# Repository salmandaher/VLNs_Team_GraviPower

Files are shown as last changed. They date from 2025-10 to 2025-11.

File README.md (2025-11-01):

# Solid-Gravity-Energy-Storage-System
Robotic Gravity-based energy storage system designed for smart cities — converts vehicle motion into storable mechanical energy and regenerates it electrically through controlled descent.

# Project Video and Report

Below is the high-quality version of the video we submitted to the WRO competition, showcasing our project in action.  
[WRO Competition Video](https://youtu.be/KDbOAnvwZOE)

You can also download and review the detailed project report we submitted:  
**[Project Report (WRO Submission)](https://github.com/salmandaher/VLNs_Team_GraviPower/blob/bfb26dfb872fea5c6c9b23eaee99e1bb86ba5fde/final%20report%20-%20VLNs.pdf)**

---

# Hi from the VLNs Team!

Welcome to our project repository. We are the VLNs team, passionate about robotics and innovation.

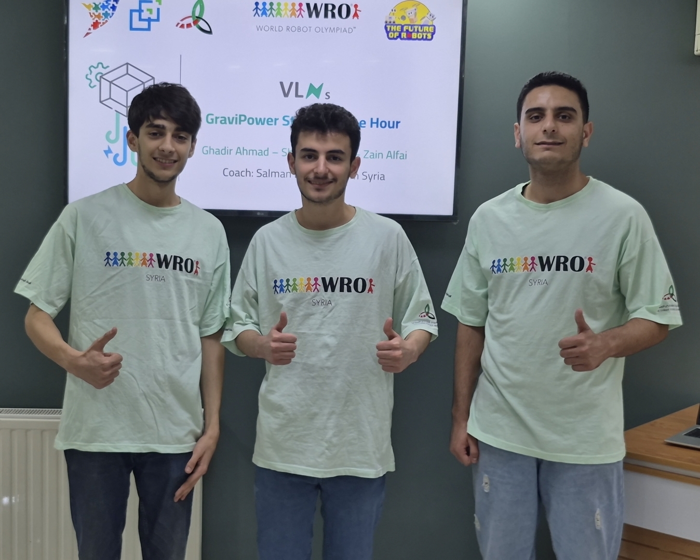
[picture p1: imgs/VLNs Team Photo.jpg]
Team Photo


Here is our coach, who has been a great mentor and guide throughout our journey:

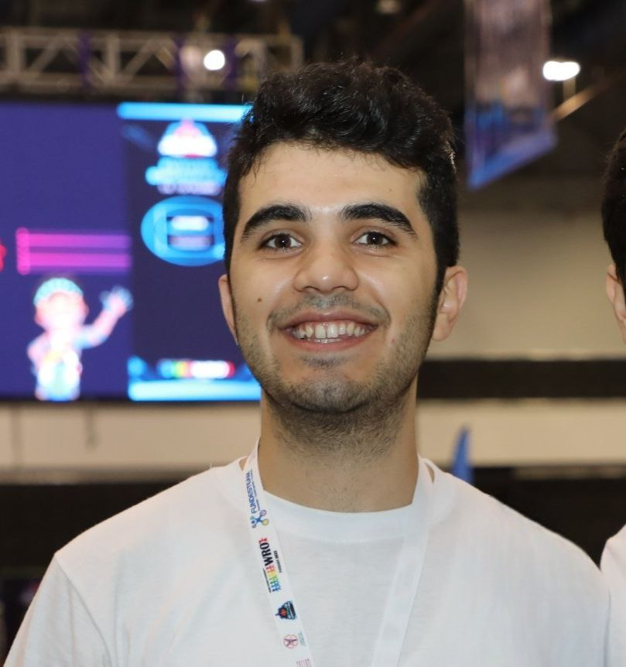
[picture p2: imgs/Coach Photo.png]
Coach Photo


---

# Full Project Photo

Full Project Photo

---

# Mechanism Design

This section provides an overview of the key mechanical components used in our project. Each mechanism plays a crucial role in ensuring efficient operation and durability. The associated STL files for 3D printing or modeling are included in the repository.

## Pseudo-Bump Mechanism Overview

The pseudo-bump functions by converting the mechanical energy from vehicles passing over it into usable energy for the system. It includes several key components that work in harmony to achieve this. The fixed joint acts as the pivot point for the bump's rotation when a vehicle passes over it. Inside this joint is an anti-reverse bearing (Rollman bearing) that prevents backward motion when the bump resets. Once a car passes, a return spring compresses under pressure and then pushes the bump back to its starting position when the vehicle leaves. The moving joint allows the bump to flatten as vehicles pass, transferring the force efficiently through the rotation of the fixed joint and maintaining system reliability.

### Fixed Joint

This contains two STL parts: the connecting plate, which connects the fixed joint to the moving joint, and the bearing holder that houses the bearing linked to the Tetrix system.  
**STL files:**  
- [First Part (Fixed Joint) STL](https://github.com/salmandaher/VLNs_Team_GraviPower/blob/d1e83de02112018f51a4b01dffcafd82a4864781/3d%20designs/Bump/first.stl)  
- [Bearing Holder STL](https://github.com/salmandaher/VLNs_Team_GraviPower/blob/d1e83de02112018f51a4b01dffcafd82a4864781/3d%20designs/stls/inner%20bearing%20to%20tetrix.stl)  

### Moving Joint

The moving joint is created between the plate with the fixed joint and another plate with a free end, which part pressed directly by vehicles.  
**STL file:**  
- [Moving Joint Linkage STL](https://github.com/salmandaher/VLNs_Team_GraviPower/blob/d1e83de02112018f51a4b01dffcafd82a4864781/3d%20designs/Bump/second.stl)  

### The Base

This holds the fixed and moving joints together, providing structural stability.  
**STL file:**  
- [Base Station STL](https://github.com/salmandaher/VLNs_Team_GraviPower/blob/d1e83de02112018f51a4b01dffcafd82a4864781/3d%20designs/Bump/station.stl)  

### Bump Motion Description

The bump moves when the free end is depressed by a passing vehicle, rotating around the fixed joint. After the vehicle passes, the return spring restores the bump to its original raised position, completing the motion cycle.

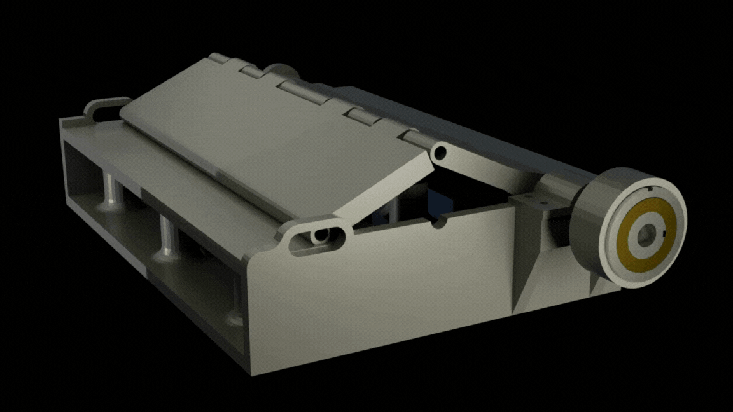
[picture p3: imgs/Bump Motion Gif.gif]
Bump Movement


---

## Motion Transmission and Torque Amplification (The Gearbox)

This part of the project is critical as it ensures efficient transfer and amplification of the torque necessary to lift the mass. The total torque amplification ratio achieved here is 10:1, an essential factor for the prototype’s performance. The motion transmission is divided into two main steps, each playing a specific role in the mechanism.

### Gearbox 

The first stage involves a gearbox with a 4:1 gear speed ratio, providing speed amplification (which is a 1:4 torque ratio). This speed amplification factor is necessary to counter the huge torque amplification factor of the next stage, keeping the torque amplification high just enough to lift the mass with the weight of the passing car.

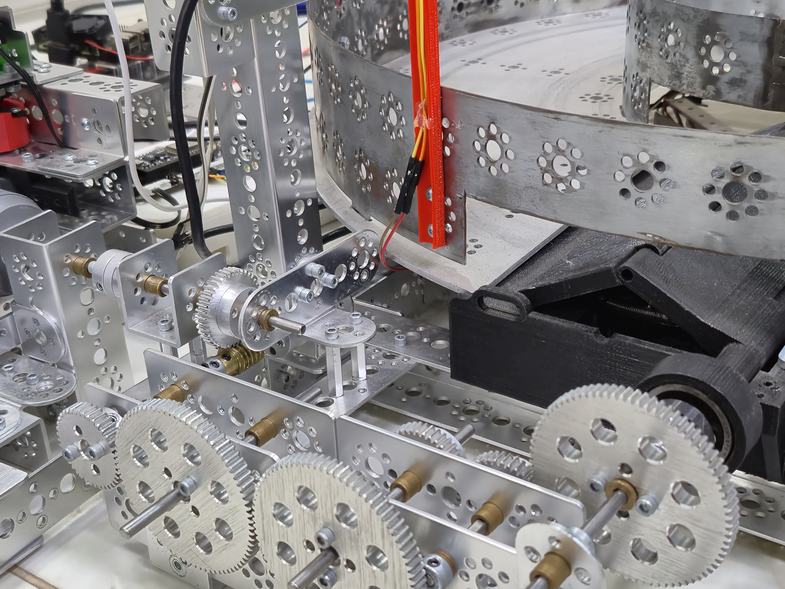
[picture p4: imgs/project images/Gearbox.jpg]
Gearbox image
 

### Worm Gear 

The second stage is a worm gear, which serves two main purposes. First, it amplifies torque with a 40:1 ratio, making it easier for the car to press the bump. Second, the worm gear acts as a self-locking mechanism, preventing the mass from falling while being lifted. This is because the worm gear cannot be driven backward by the gear connected to it; it only transmits motion forward, thus securing the mass position reliably.

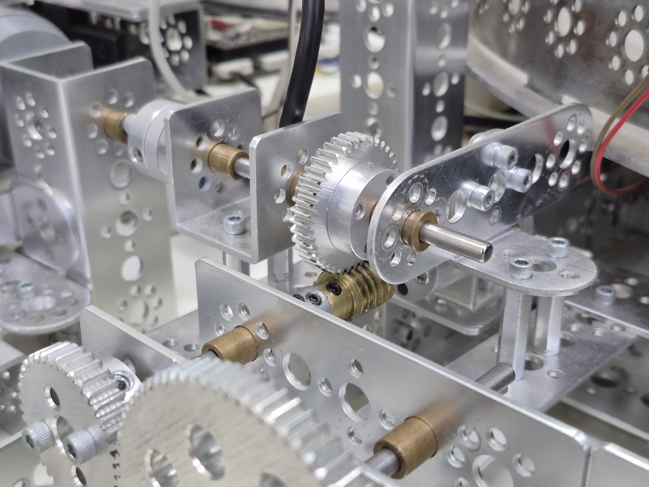
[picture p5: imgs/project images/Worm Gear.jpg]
Worm gear image


---

## Lifting System

The lifting system is responsible for managing the vertical movement of the mass with precision and stability. It consists of three main components:

### Main Pulley (Spool)

This is the central pulley around which the rope winds. Its radius directly affects the torque experienced in the system, playing a key role in the mechanical advantage and energy efficiency. During the project, we designed and tested three main versions of this pulley to optimize performance and durability.

**STL files:**  
- [Version 1 Pulley STL](https://github.com/salmandaher/VLNs_Team_GraviPower/blob/a61094ec972bfa96dd2c8d812677eebc3b2d72a3/3d%20designs/stls/Pulley%20v1.0-01.stl)  
- [Version 2 Pulley STL](https://github.com/salmandaher/VLNs_Team_GraviPower/blob/a61094ec972bfa96dd2c8d812677eebc3b2d72a3/3d%20designs/stls/Pulley%20v1.0-03.stl)  
- [Final Pulley Design STL](https://github.com/salmandaher/VLNs_Team_GraviPower/blob/a61094ec972bfa96dd2c8d812677eebc3b2d72a3/3d%20designs/stls/Pulley%20v3.2.stl) 

### Guiding Pulleys

Two guiding pulleys are installed at the top of the tower. Their main function is to route the rope correctly, ensuring it remains aligned throughout the lifting and lowering operations.

**STL file:**  
- [Guiding Pulley STL](https://github.com/salmandaher/VLNs_Team_GraviPower/blob/a61094ec972bfa96dd2c8d812677eebc3b2d72a3/3d%20designs/stls/direction_pulley.stl)

### Mass Pulley

Attached directly to the mass, this pulley serves multiple purposes: it protects the rope from excessive wear, improves the stability of the mass during motion, and doubles the torque applied when lifting. This crucial component helps regulate the discharge time, improving system reliability.

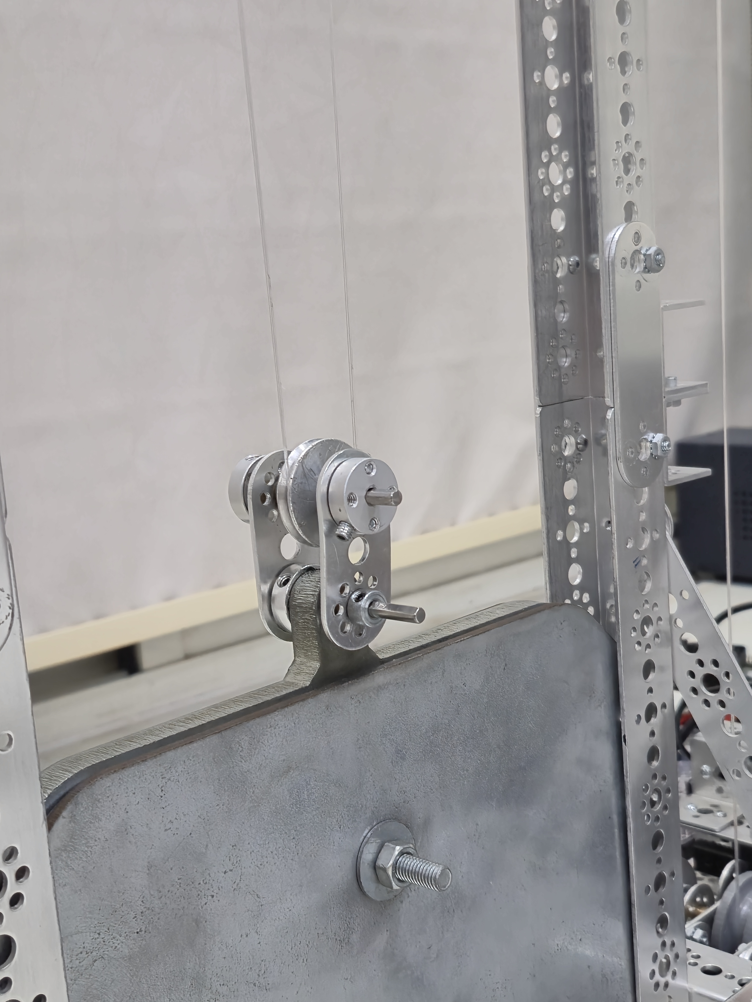
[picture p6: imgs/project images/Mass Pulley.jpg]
Mass pulley image


---

## Connecting and Disconnecting Mechanism

To switch to the discharging mode, the main pulley should be disconnected from the gearbox and connected to the energy generation system, which consists of the motor and its dedicated gearbox. This requirement led to the development of a specialized mechanism for connecting and disconnecting.

The core component consists of 3D-printed PLA parts that resemble circular saw-tooth gears designed to transfer energy unidirectionally. When the main pulley is shifted towards the gearbox side, two opposing saw-tooth parts engage, allowing the gearbox to drive the pulley. Conversely, when the pulley is pushed in the opposite direction, the saw-tooth parts disengage on the gearbox side and engage on the motor side gearbox, thus transferring motion to the motor side.

To facilitate movement between these two positions, we utilize an HTS-35H Servo motor with a torque capacity of 35 kg ·cm. This servo motor is connected to a rack and pinion mechanism that converts the servo’s rotational motion into linear motion, enabling precise and reliable movement of the connecting and disconnecting assembly. The servo is controlled by an ESP32 core board alongside a multifunctional extension board for efficient operation.

### Saw-Tooth Gears

These saw-tooth gears are the key elements that allow unidirectional energy transmission during connection and disconnection. The design includes two complementary halves to ensure smooth engagement and disengagement.

**STL files:**  
- [Saw-Tooth Gear Half 1 STL](https://github.com/salmandaher/VLNs_Team_GraviPower/blob/a61094ec972bfa96dd2c8d812677eebc3b2d72a3/3d%20designs/stls/Coupler%20V2.0-2.stl)  
- [Saw-Tooth Gear Half 2 STL](https://github.com/salmandaher/VLNs_Team_GraviPower/blob/a61094ec972bfa96dd2c8d812677eebc3b2d72a3/3d%20designs/stls/Coupler%20V2.0.stl)

Here is a simulation demonstrating the engagement and disengagement process of the saw tooth gear:
Tooth Gear Motion

### Rack and Pinion Mechanism

The rack and pinion mechanism translates the servo motor’s rotational motion into linear displacement. The pinion, rotated by the servo, engages with the rack teeth to produce controlled linear movement. This mechanism enables the precise shifting required to connect or disconnect the main pulley from either gearbox side.

**STL files:**  
- [Rack STL](https://github.com/salmandaher/VLNs_Team_GraviPower/blob/a61094ec972bfa96dd2c8d812677eebc3b2d72a3/3d%20designs/stls/39300B_TXM-Linear%20Slide%20Rail.stl)  
- [Pinion STL](https://github.com/salmandaher/VLNs_Team_GraviPower/blob/a61094ec972bfa96dd2c8d812677eebc3b2d72a3/3d%20designs/stls/39300A_TXM-Linear%20Slide%20Gear.stl)

Below is a simulation illustrating the full operation of the connecting and disconnecting mechanism:
C&D Full Mechanism Motion

---

## Motor Gearbox
The motor gearbox is set to adjust the motor output speed and torque to a desired level. It applies a 1.5 speed amplification factor, combined with the 2:1 speed amplification applied by the mass pulley system, the total becomes a 3:1 speed amplification factor, rotating the motor from the mass's fall to produce higher voltage values.  

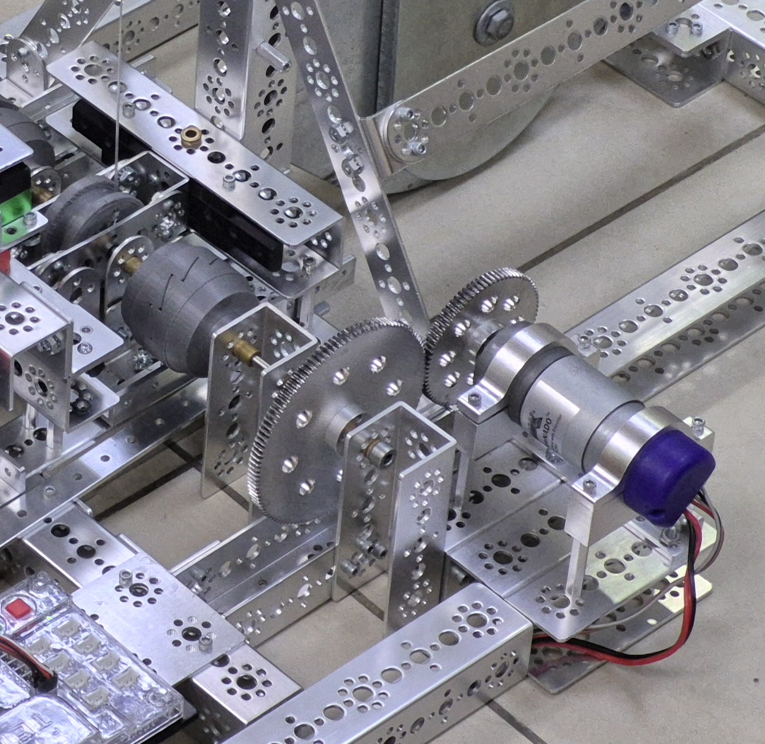
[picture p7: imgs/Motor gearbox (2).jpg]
Motor Gearbox


---

# The coding of the solution
## The main control code (the Python code)

running on the Raspberry Pi 4 device, this Python code serves as the central control unit for our system. It manages the system’s operational states, including charging, discharging, and fast charge modes, by coordinating commands to various controllers such as the PRIZM and the ESP. The code continuously monitors sensor data to make decisions that ensure smooth transitions between modes and optimize system performance. Additionally, it implements a PID control algorithm to regulate the descent speed of the mass, maximizing energy generation efficiency by dynamically adjusting the electrical load without wasting energy through conventional braking. The program also supports real-time monitoring and manual mode control via a connected web-based interface, enabling effective management of the entire energy storage process.

### Main Tasks of the Python Control Code

The Python script performs critical functions to optimize the operation of the gravity-based energy storage system:

1. It calculates the generator's rotational speed during discharging using encoder feedback.
2. It applies a PID (Proportional-Integral-Derivative) control algorithm to regulate the generator speed at the point of maximum power generation efficiency. The PID output is fed to the PWM BTS driver to dynamically adjust the electrical load. The general form of a PID controller is expressed as:

$$
u(t) = K_p e(t) + K_i \int_0^t e(\tau) d\tau + K_d \frac{d e(t)}{d t}
$$

Where:

- $$\( u(t) \) $$ is the control signal output,
- $$\( e(t) \) $$ is the error between target and actual speed,
- $$\( K_p \) $$ is the proportional gain,
- $$\( K_i \) $$ is the integral gain,
- $$\( K_d \) $$ is the derivative gain.

3. It counts the number of vehicles passing over the pseudo-bump to track energy input events.
4. It estimates the current height of the lifted mass by correlating the vehicle count and encoder data using the equation:

$$
h = N_{cars} \times h_{car} - \Delta E \times h_{encoder}
$$

   Where:

   - $$\( h \) $$ is the current height of the lifted mass
   - $$\( N_{cars} \) $$ is the number of cars passing over the pseudo-bump
   - $$\( h_{car} \) = $$ is the height increment per car press (how much one car lifts the mass)
   - $$\( \Delta E \) = $$ is the change in encoder readings during the last discharge
   - $$\( h_{encoder} \) = $$ is the height decrement per encoder pulse (how much one encoder pulse corresponds to the mass descending)

   This equation estimates the net height of the mass by aggregating the lifting increments caused by passing cars
   and subtracting the descent quantified by encoder pulses during discharging.
   
5. Based on the mass height and ambient lighting conditions, it determines the system's operating mode: switching to "maxCharge" when the mass height exceeds 105 units, entering "discharge" mode at night, and defaulting to "charge" or manual mode as selected through the dashboard interface.

### Code Explanation Flowchart
Below is a flowchart illustrating the workflow and main components of the code:

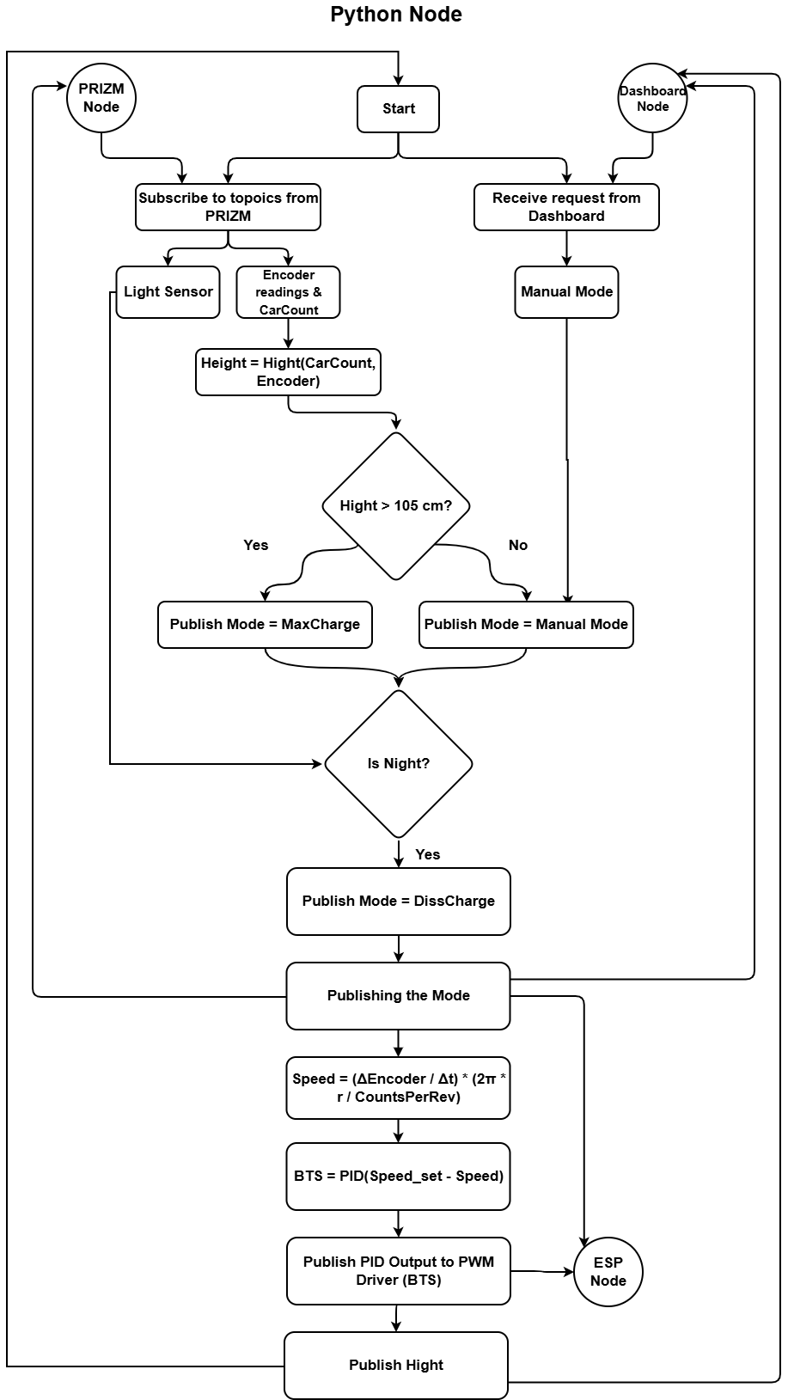
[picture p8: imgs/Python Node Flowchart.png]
Flowchart


### Code
You can view the full code [here](https://github.com/salmandaher/VLNs_Team_GraviPower/blob/main/src/vlns/src/serverna.py).

---

## The PRIZM code:
The PRIZM code is responsible for directly interfacing with hardware components to support the energy storage system's operation. It continuously reads encoder feedback to monitor the generator's rotational position and speed. The code controls the generator, turning it on during the fast charge mode and off during discharging. It detects when a car passes over the pseudo-bump to coordinate energy accumulation events. Furthermore, it manages the servo motor that controls the bump's state, flattening (deactivating) it when not charging and activating it during charging. Lastly, the PRIZM code reads ambient lighting sensor feedback to help determine system modes based on day/night conditions.

### Main tasks of the PRIZM code:

1. Reading encoder feedback for generator monitoring.
2. Controlling the generator state (activated during fast charge mode, deactivated during other modes).
3. Detecting cars passing over the pseudo-bump.
4. Managing the bump-servo motor to flatten or activate the bump based on the mode.
5. Reading the lighting sensor to support automatic mode switching.

### Code Explanation Flowchart
Below is a flowchart illustrating the workflow and main components of the code:

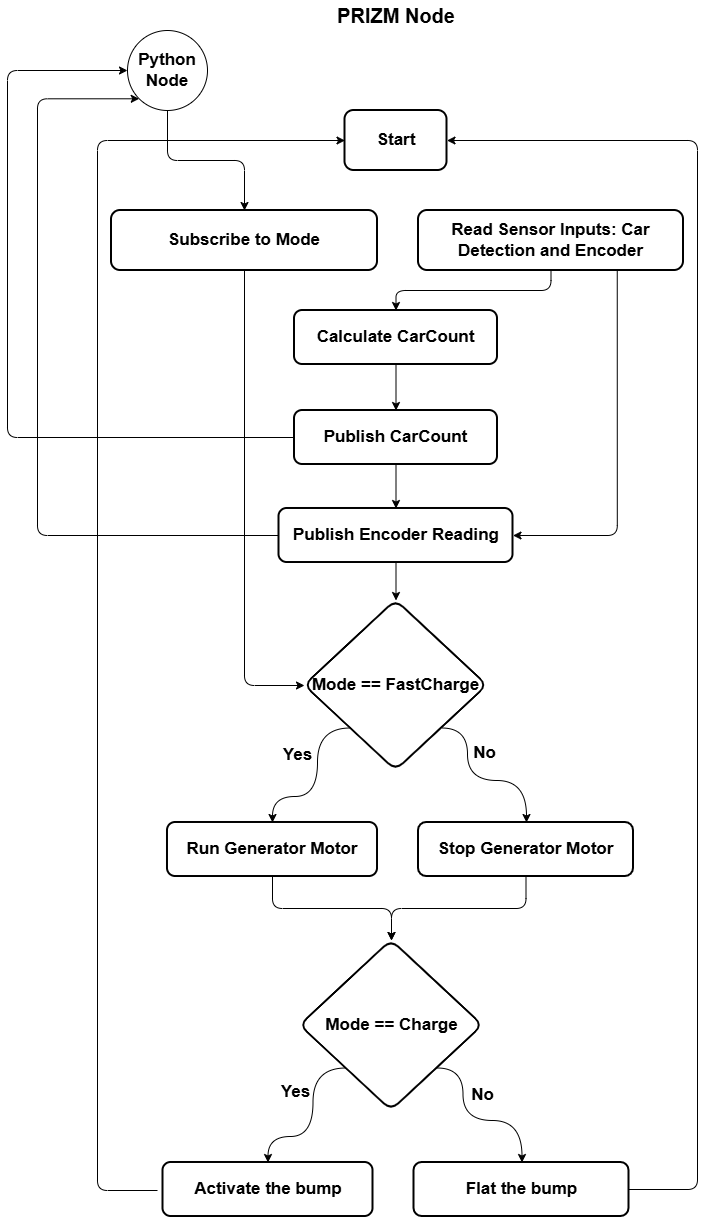
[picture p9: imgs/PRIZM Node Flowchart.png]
Flowchart


### Code
You can view the full code [here](https://github.com/salmandaher/VLNs_Team_GraviPower/blob/main/src/vlns/src/PRIZM_node/PRIZM_node.ino).

---
## The ESP code:
The ESP code functions as the core controller for mechanical and electrical actuations within the energy storage system. It manages the disconnecting and connecting mechanism, dynamically linking the main pulley to the generator during discharge or fast charge modes, and to the gearbox in charge or max charge modes. The code also controls the electrical load system by activating the LED lights during discharge mode and deactivating it otherwise. Furthermore, the ESP code modulates the PWM driver (BTS), adjusting the electrical load on the generator in response to PID control signals computed externally, ensuring precise and efficient energy management.

### Main tasks of the ESP code:

1. Control the disconnecting and connecting mechanism, linking the main pulley to the generator or gearbox based on system mode.
2. Manage the electrical load system indicator light, turning it on only during discharge mode.
3. Regulate the PWM driver (BTS) to adjust the electrical load on the generator using PID output from the Python controller.

### Code Explanation Flowchart
Below is a flowchart illustrating the workflow and main components of the code:

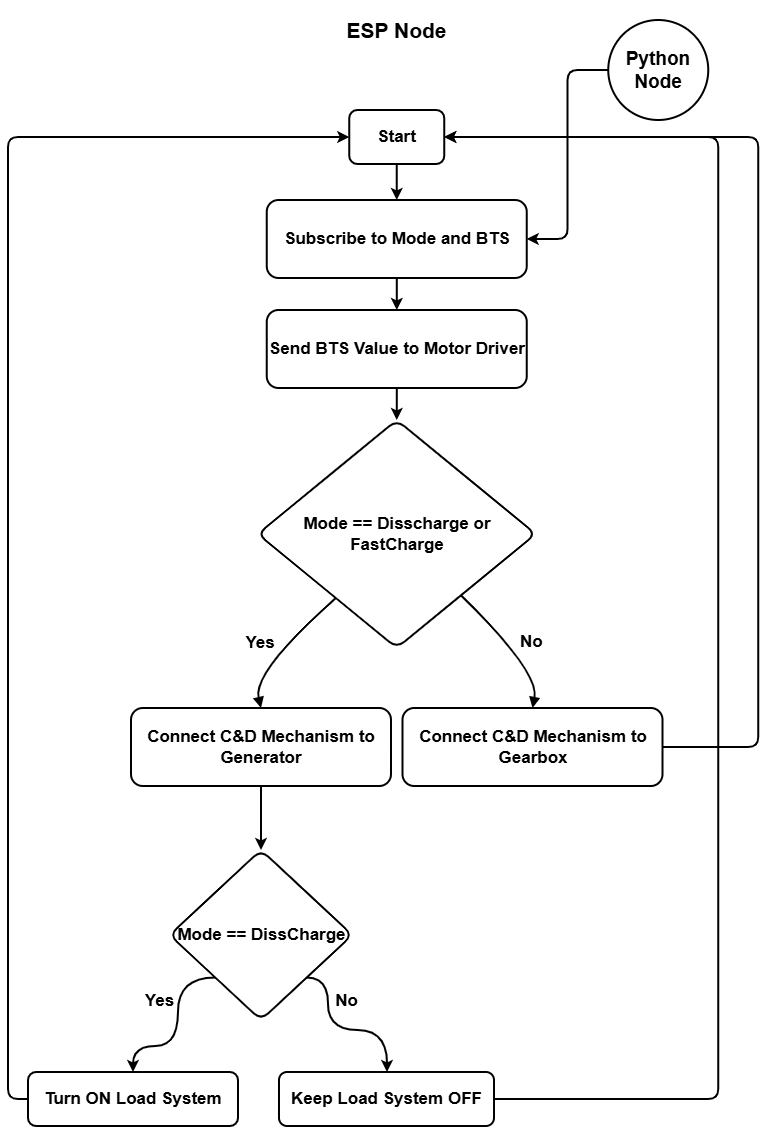
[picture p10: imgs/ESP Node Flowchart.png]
Flowchart


### Code
You can view the full code [here](https://github.com/salmandaher/VLNs_Team_GraviPower/blob/main/src/vlns/src/Esp_Node/Esp_Node.ino).

---
## The Dashboard codes:

The Dashboard integrates frontend and backend components to provide a real-time, interactive user interface for the energy storage system. It combines HTML for structure, a custom CSS stylesheet for tailored styling and responsive design, and Node.js for backend communication management using server-side JavaScript. This interface displays current system status metrics, such as the height of the mass and the number of cars passing over the bump, and allows users to manually select or override operating modes through an intuitive interactive dashboard.

### Main tasks of the Dashboard:

1. Display system status in real time, including key metrics like mass height and vehicle count.
2. Enable users to change operating modes manually via an interactive interface.

### Code Explanation Flowchart
Below is a flowchart illustrating the workflow and main components of the code:

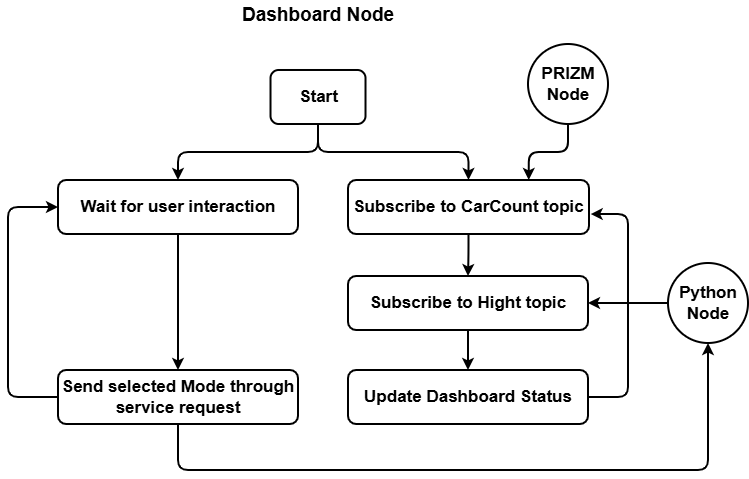
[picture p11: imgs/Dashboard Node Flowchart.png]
Flowchart


### Code Links:
You can view the codes here: 
- [HTML Code](https://github.com/salmandaher/VLNs_Team_GraviPower/blob/main/src/Web%20Dashboard/public/New/index3.html)
- [CSS Code](https://github.com/salmandaher/VLNs_Team_GraviPower/blob/main/src/Web%20Dashboard/public/New/style.css)
- [Node.js Code](https://github.com/salmandaher/VLNs_Team_GraviPower/blob/main/src/Web%20Dashboard/app.js)

---
# ROS Implementation

Since our project involves multiple controllers and a web-based dashboard, we implemented the concept of **ROS (Robot Operating System)** to facilitate communication between these controllers and maintain an organized and synchronized system workflow. The ROS version used in this project is **ROS 1 (Noetic)**

In the following sections, we explain the ROS structure that underpins the operation of our project — including detailed descriptions of each ROS node, how the nodes communicate with one another, and the types of information exchanged between them.

## Introduction

Our ROS system consists of four main nodes that communicate with each other to manage the overall functionality of the project, these nodes are in the **vlns** ROS package in the catkin workspace:

- **Python Node:**  
  Runs a Python program that serves as the central control of the system. It performs key calculations and manages the behavior of other nodes through ROS communication.

- **PRIZM Node:**  
  Executes an Arduino program that reads data from various sensors and controls the actuator used as a generator. It functions as an endpoint in the ROS communication network.

- **ESP Node:**  
  Runs another Arduino program that serves as an additional endpoint in the ROS communication structure, handling specific sensing or control tasks.

- **Dashboard Node:**  
  Responsible for displaying system values obtained from the controllers’ sensor readings. It also allows manual mode switching to adjust system behavior.

The following **rqt graph** illustrates the communication links and message flow between the nodes in our ROS system, which will be explained in detail later on:

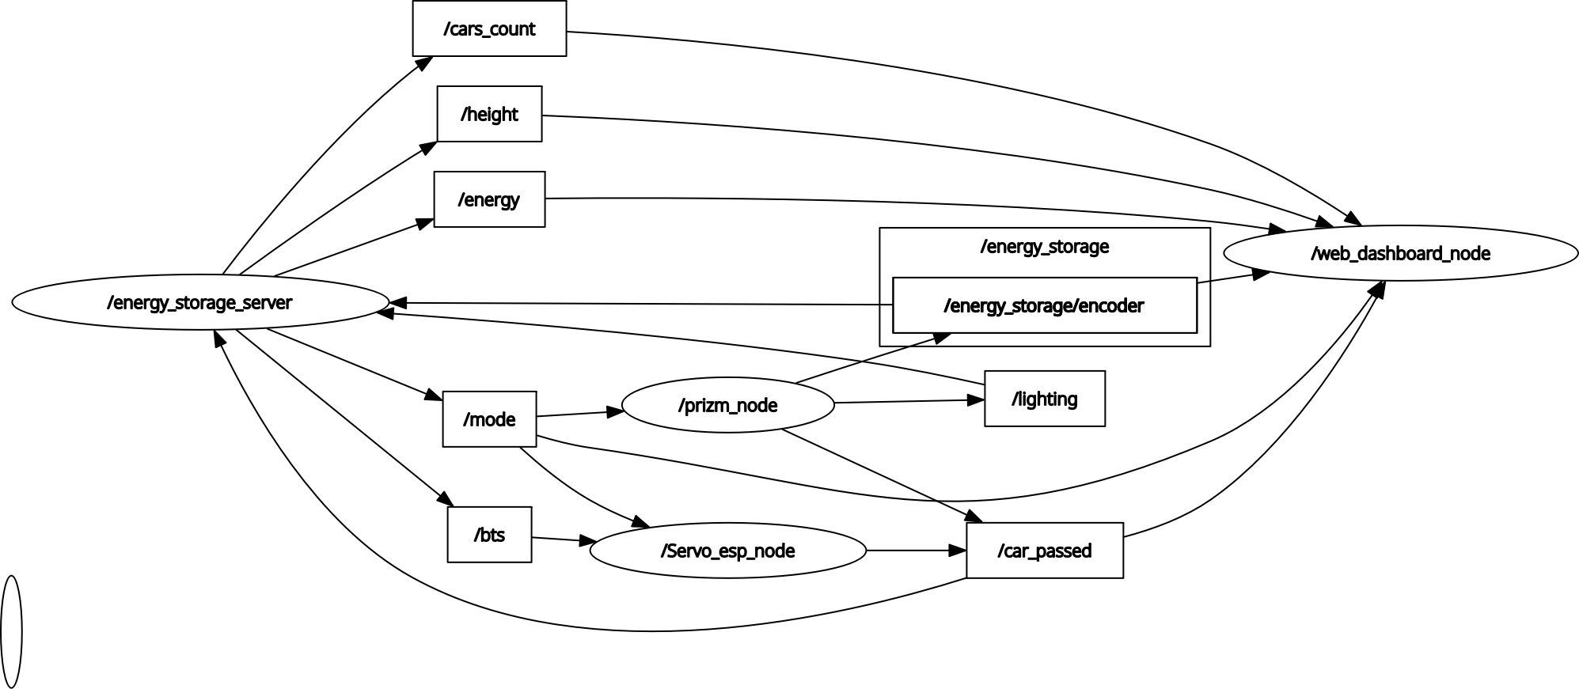
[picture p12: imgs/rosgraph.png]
ROS Node Graph


To start the project, we open a terminal and launch the **ROS master** using the following command:
```bash
roscore
```
After that, each node should be started separately in a new terminal tab.
Before running any node, we source the terminal from the catkin workspace:
```bash
Source devel/setup.bash
```

---

## Python Node

The **Raspberry Pi** device (**Raspberry Pi 4**, running **Debian Bookworm**) serves as the **ROS Master** in our system. It hosts the main Python node that manages communication and coordination among all other nodes through various **services**, **publishers**, and **subscribers**.

### Services
- **Mode Service:**  
  The Python node participates in a mode management service with the Dashboard node.  
  When the mode is changed manually from the Dashboard, the Dashboard node sends a service request to the Python node containing the selected mode in the request message.  
  The Python node then updates the global variable representing the current mode and returns a success response to the Dashboard node.

We built our own **custom service structure**, which includes:  
- A **string variable** in the request message to specify the selected mode.  
- A **boolean variable** in the response message that returns `true` to indicate successful operation.  

You can view the service structure file [here](https://github.com/salmandaher/VLNs_Team_GraviPower/blob/main/src/vlns/srv/sges.srv).

### Publishers
- **`/mode`:**  
  The Python node continuously publishes the current mode to all other nodes, ensuring system-wide synchronization and state consistency.

- **`/height`:**  
  The node calculates the height of the mass based on sensor data and publishes it for display on the Dashboard.

- **`/cars_count`:**  
  The code tracks the number of times the bump push button is activated and publishes this value to be displayed on the Dashboard.

- **`/bts_value`:**  
  The node processes mass falling speed readings, applies a PID algorithm to compute the BTS value, and publishes it to control the BTS system—optimizing load management and fall speed.

### Subscribers
- **`/encoder`:**  
  Receives encoder data for BTS value and height calculations.  
- **`/car_passed`:**  
  Monitors signals indicating that a car has passed over the bump.  
- **`/light_sensor`:**  
   Reads light intensity data for use in mode adjustments.

### Communication with the ROS Master
The Python code runs as a ROS node on the Raspberry Pi. It registers with the ROS master using the ROS network protocol (ROS Master URI). The node uses ROS client libraries (rospy) to publish and subscribe to topics, provide or call services, and interact with other ROS nodes.

This is the terminal command for initiating the connection.
```bash
rosrun vlns serverna.py
```
---

## PRIZM Node

The **PRIZM node** is one of the two nodes in the system running Arduino code.  
The program on the PRIZM controller is responsible for several key tasks, in addition to participating in multiple ROS communications with other nodes.

### Publishers
- **`/encoder`:**  
  The PRIZM node reads the encoder values from the TorqNedo motor used as a generator and publishes them. These readings are used by the Python node for height and speed calculations.

- **`/light_sensor`:**  
  This node publishes data from the light sensor, which is subscribed to by the Python node to trigger the system’s autonomous behavior.

- **`/car_passed`:**  
  The code monitors the push button mounted on the bump and detects when it is pressed (FALLING state). These readings are published and subscribed to by other nodes in the system to track passing vehicles.

### Subscribers
- **`/mode`:**  
  The node subscribes to the mode topic published by the Python node. It adjusts its behavior based on the current mode — whether the system is **charging**, **discharging**, or **fast charging**.

### Communication with the ROS Master
The **PRIZM node** communicates with the **ROS Master** via a USB serial connection on port `/dev/ttyUSB0` with a baud rate of **57600**.  

To initiate this connection, we use the following terminal command:
```bash
rosrun rosserial_python serial_node.py /dev/ttyUSB0 _baud:= 57600
```
---

## ESP Node

The **ESP node** is another endpoint in the ROS communication system running Arduino code.  
It is responsible for controlling the switching mechanism and managing the load on the generator, which requires key information from other ROS nodes.

### Subscribers
- **`/mode`:**  
  Similar to the PRIZM node, this node subscribes to the **mode** topic published by the Python node.  
  It adjusts its behavior dynamically based on the current mode updates received from the ROS network.

### Communication with the ROS Master
The **ESP node** communicates with the **ROS Master** over a **TCP connection via Wi-Fi**.  
It connects to the Raspberry Pi device at the IP address **192.168.43.47** through **port 11411**, with a baud rate of **115200**.

This is the terminal command for initiating the connection.
```bash
rosrun rosserial_python serial_node.py tcp _baud:=115200
```
---

## Dashboard Node

The **Dashboard node** is an essential component of the ROS network that allows users to monitor system values and manually control its behavior.  
It participates in multiple ROS communications with other nodes to ensure accurate data display and responsive control.

### Services
- **Mode Service:**  
  When the user changes the mode manually using one of the mode buttons on the dashboard, the Dashboard node sends a service request to the Python node.  
  This request updates the global system mode to the newly selected one.

### Subscribers
- **`/mode`:**  
  The system mode can be changed either autonomously by internal system processes or manually from the dashboard.  
  In both cases, the Dashboard node subscribes to the **mode** topic published by the Python node and displays the current mode.  
  This ensures system synchronization and helps in detecting communication or logic errors.

- **`/car_passed`:**  
  Subscribes to the **car_passed** topic published by the PRIZM node and displays real-time status updates indicating when a car passes over the bump.

- **`/cars_count`:**  
  Subscribes to the **cars_count** topic (published by the PRIZM node) and displays the total number of cars that have passed over the bump since the system started.

- **`/height`:**  
  Subscribes to the **height** topic published by the Python node and displays the current height of the mass on the dashboard.

### Communication with the ROS Master
The dashboard is a web interface accessible from any device on the network. The dashboard web client connects to the ROS master through a Socket.IO server, which runs on the Raspberry Pi. It connects with the IP address of the Raspberry Pi on the network through port 3000.

This is the terminal command for initiating the connection.
```bash
node app.js
```

---

## Launch File

To simplify the process of running the project, we created a **launch file** — [**sges.launch**](https://github.com/salmandaher/VLNs_Team_GraviPower/blob/main/src/vlns/launch/sges.launch) — which automatically starts all the required nodes.  

After running the **roscore** and sourcing the terminal, we launch the entire system with a single command:
```bash
roslaunch vlns sges.launch
```
---
# Business Calculations
## Payback Time and Annual Revenue Calculation

The project's annual revenue from produced electricity is calculated using:

$$
R_{year} = \frac{E_{year}}{1000} \times 128.8
$$

Where:
- $R_{year}$ is the yearly revenue in dollars.
- $E_{year}$ is the total energy generated yearly in watt-hours (Wh).
- 128.8 is the price in dollars per 1000 kWh (where 1 kWh = 1000 Wh).

The payback time $T$ (in years) is calculated as:

$$
T = \frac{\text{Total Project Cost}}{R_{year}}
$$

Where:
- **Total Project Cost** is the full installation and equipment cost.
- $R_{year}$ is as defined above.

### Example:

If your system generates $E_{year} = 40\,000$ Wh per year, the yearly revenue is:

$$
R_{year} = \frac{40\,000}{1000} \times 128.8 = 40 \times 128.8 = 5\,152\,\text{USD}
$$

If the total project cost is $59\,000$ USD, the payback time is:

$$
T = \frac{59\,000}{5\,152} \approx 11.46\,\text{years}
$$

## ROI Calculation Method

ROI formula for your project:

$$
ROI = \frac{\text{Net Profit}}{\text{Cost of Investment}} \times 100
$$

## Real-Example Study

- **Power used per day:** $17\, \text{LEDs} \times 40\,\text{W} \times 6\,\text{h} = 4,080\,\text{Wh/day} = 4.08\,\text{kWh/day}$
- **Yearly usage:** $4.08\,\text{kWh/day} \times 365 = 1,489.2\,\text{kWh/year}$
- **Annual value at $128$/1,000 kWh:** 
  $$
  \text{Annual Value} = \frac{1,489.2}{1,000} \times 128 = \$190.63
  $$

### Homs City Data

- **Total investment cost:** \$8,648
- **Annual energy output:** $1,489.2\,\text{kWh/year}$
- **Estimated benefit:** $\$190.63$

### ROI for Year 1:

$$
ROI_{\text{Year 1}} = \frac{190.63}{8,648} \times 100 \approx 2.2\\%
$$

### ROI After 2 Years

Assuming similar annual revenue, the ROI after 2 years is:

$$
ROI_{\text{Year 2}} = \frac{2 \times 190.63}{8,648} \times 100 \approx 4.4\\%
$$

This assumes revenue accumulates linearly and no extra costs occur during the 2 years.

---

# Project Challenges

## Tower Design Evolution

Throughout the project's development, the tower structure underwent multiple design iterations due to various challenges. Below are three old versions of the tower with explanations on why each was changed:

### Version 1
Tower Version 1
The first version of the tower was made with a simple concept, four main columns where each two adjacent columns are connected with each other with flat beams.

### Version 2
Tower Version 2
The first version of the tower was somehow steady, but to increase its stability according to engineering concepts we removed the straight beams that connect every two adjacent channels and replaced them with triangular connections, to increase stability and efficiency reaching the second design version of the tower.

### Version 3
Tower Version 3
The second version seemed to work well at first, but we faced some problems with sitting it without tilting, it also costs too many Tetrix parts, which made us think of a solution for this problem leading us again to the third and final version of the tower, having a strong base to correct tilting, and high efficiency using fewer Tetrix parts.

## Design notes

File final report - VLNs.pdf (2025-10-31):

# Senior

# VLNs

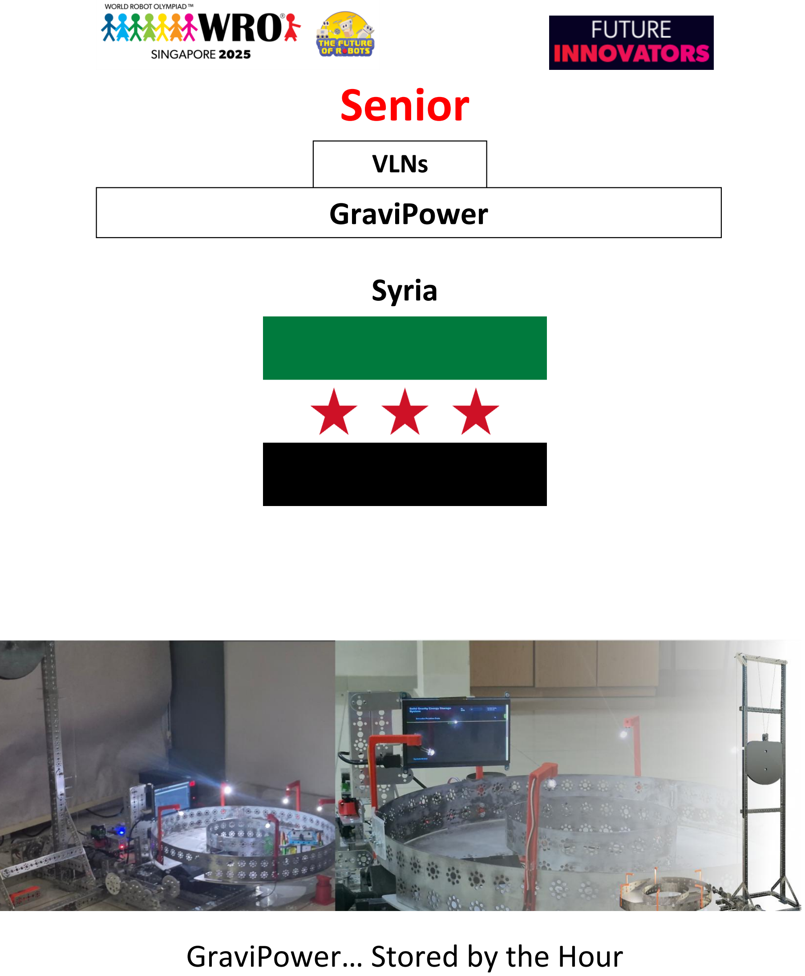
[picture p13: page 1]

# Syria

# GraviPower… Stored by the Hour

# GraviPower

## WRO 2025 | FUTURE INNOVATORS (SENIOR)

## VLNs Team

# TABLE OF CONTENTS

We are the VLNs, a team of three passionate students from the National Center for the Distinguished (NCD). Over the past three years, we have participated in major competitions, earning valuable experience and insight along the way. After working together for so long, we ’ve become more than just teammates, we ’ve become a small family. Now, we aim for the gold! During our time at the NCD, we lived, studied, and grew together. Each of us has improved his skills and learned to overcome challenges, and now we complement one another perfectly. Interestingly, our team ’s name, VLNs, comes from a game we love, but it also stands for Vertical Lifting Newtons, which gives a little description of our project.

Meet the Team:

- Ghadir Ahmad (18 years old): With a strong foundation in mechanics and CATIA V5, Ghadir played a crucial role in construction and 3D designing. His innovative thinking and helpful nature contributed to many creative ideas along the way.
- Shady Al-Hasan (19 years old): Played an important role in developing the project mechanically also using CATIA V5, in addition to being the best coder in the team. Shady provided us with cutting-edge solutions and worked tirelessly through tough times to ensure the success of our project.
- Zain Alfai (19 years old): Zain was a major contributor to the mechanical and physical foundations on which our project is built. In addition to being our circuit designer, he supported the team with his hands-on skills and contributed valuable ideas throughout the project.
- Salman Daher - Coach (21 years old): Salman graduated from the National Center for Distinguished and now studies robotics engineering at Manara University. Salman gave us a lot of advice. His passion for learning and sharing knowledge inspires everyone around him. In addition, he was in the first place our Mathematical Modelling trainer.

## Figure 1: Team’s photo

# TEAM PRESENTATION

In our modern world, renewable and non-renewable energy sources are diverse, from solar energy to wind and wave energy etc. The high availability of energy and the instability of its generation, such as solar and wind energy, makes the biggest problem today lies in energy storage rather than its generation. Hence the importance of our solution, which provides a sustainable, effective, durable, and high-capacity way to store energy, which is Solid Gravity Energy Storage [1].

The idea is to raise a large mass to a high altitude above the ground. It can be lifted inside a high tower or inside mines and wells. When the potential energy stored in this mass is needed, the mass is left to fall and rotate a generator while falling to produce electricity with high efficiency (80% - 90%) [2]. Thus, the mass plays the role of a battery [3].

And one fascinating thing is that our system does not use electricity for charging. but provides free electricity, by raising the mass purely mechanically.

One promising source of untapped energy suitable to do this is all around us - something we experience every day: the movement of vehicles. We designed a clean car pseudo-bump that transmits the power of the movement of vehicles and utilizes it to raise a huge mass. But how can a car raise such a massive weight? We implemented a one-way gearbox to solve this issue; this gearbox increases the torque of the car so it can raise the mass. Our solution falls under the first area of the competition theme for this year. Specifically, the second sub-area (Robots Helping to Save Resources) as it has helped save city resources and protect the environment.

But of course, the mass falls at an accelerated rate due to the acceleration of gravity, and the generator rotating at an accelerated speed will cause unstable and inefficient generation. We can resort to breaking the mass in order to slow it down, but that is not the ideal solution because it causes energy loss. Here comes the role of our robotic solution, which operates an electric brake to slow down the mass ’s fall and regulate its descending speed. We use controllers and sensors to increase the electrical load on the generator when the falling speed increases, which leads to its slowing down. In this case, there is no wasted energy, because the energy is used to operate the excess load, which may be represented by several useful devices.

Providing a solution to one of the major problems of today ’s world, which is energy storage, our project presents an innovative idea that, if applied in real life, could represent a significant step towards a cleaner and more sustainable future. Our project ’s efficient use and harvesting of energy reinforces its importance in saving city resources by making use of different forms of energy around us [4].

What did we get in our prototype with 11.2 Kg mass and 1.2m tower height?

1) 6 Street Lights
2) 2 DC Motors Overload
3) 3.5 watt/s ~ 1Kwatt/h
4) 35s Operation Time

# EXECUTIVE SUMMARY

The Base of The Idea:

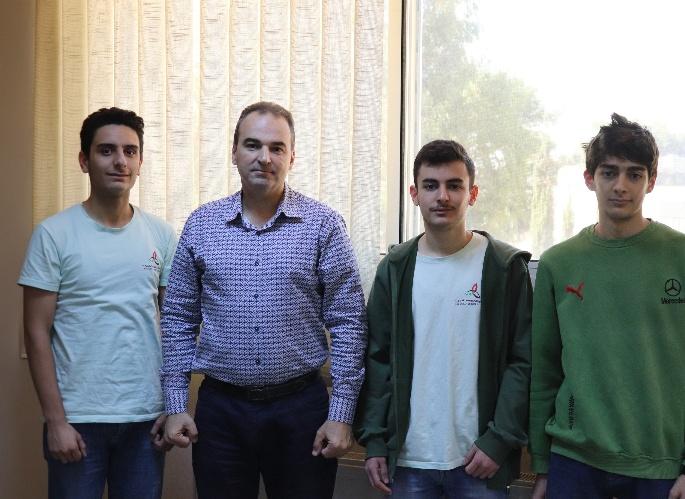
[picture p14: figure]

At the beginning of thinking about an innovative idea, our team met with Dr. Almohannad Makki, the former manager of the National Center for the Distinguished in Syria, to discuss some different and new ideas that could contribute to solving a problem in an environmentally clean way. After a while of discussion and searching, we settled on the idea of storing energy using solid gravity. This idea seemed to us to be an appropriate and strong basis for launching our project, due to its benefits on various social, economic, and environmental levels. Few other research has been made, before we settled on the idea of raising a mass from the ground, thus, storing its potential energy, and when the energy is needed, the mass is left to fall and rotate a motor as it is falling, to retrieve the energy back.

Efficiency Enhancement:

After a period of testing this idea and studying its details, we found that investing energy from the falling mass can be greatly improved if we can control the mass to fall at a constant speed. Controlling the speed of the mass is possible using brakes, but the enhancement we found is that we can cancel the use of brakes by increasing the electrical load on the motor, which will slow it down and form a brake to control the speed of the mass, and that is how the energy is utilized and not wasted like in a normal mechanical brake, this idea is the key innovation of our project.

Energy Accumulation:

After that, and in the context of our attempt to make the project more renewable and environmentally friendly, we thought of ways to lift the suspended mass on a tower.

We tested several types of energy for the lifting process until we arrived at the idea of taking advantage of the cars ’ movement. When considering the heavy traffic congestion. This idea is excellent as a large and stable energy source.

We conducted extensive research into existing gravity-based energy storage systems and found several projects with concepts like ours. Companies like Energy Vault (https://www.energyvault.com/#:~:text=We%20are%20the%20only%20energy%20storage%20company) and Gravitricity (https://gravitricity.com/#:~:text=At%20Gravitricity%20we%20are%20developing) have developed systems that lift heavy weights to store potential energy, which is later converted into electricity when the weights descend. Energy Vault uses cranes to lift large concrete blocks [5], while Gravitricity employs winches

# ROBOTIC SOLUTION

### 3.1 EVOLUTION OF PROJECT IDEA DURING THE PREPARATION

### Figure 2: VLNs Team with the Former Head of the National Center for Distinguished - Dr. Almohannad Makki

### 3.2 RESEARCH INTO SIMILAR IDEAS

to raise weights in mines shafts [6]. Additionally, regenerative braking systems in electric vehicles, which capture energy from braking, are like our method of harnessing energy from car movement [7].

Our project is distinct primarily due to the high efficiency of our energy accumulation process by taking the energy from the cars purely mechanically. We have developed a smart method of controlling the descent of the mass by adjusting the electrical load on the motor to act as a brake [8], maximizing energy generation during the falling phase. This makes our power retrieval more efficient compared to other systems. Additionally, we combine this with an innovative energy generation approach, where car movement over pseudo-bumps helps lift the mass. This integration of energy storage and generation provides a

sustainable, dual-function system that sets our design apart.

The mechanics in our prototype are basically the hardware of each of the charging phase (when the mass rises) and the discharging phase (when the mass descends), we will break down and explain the mechanics of both phases, starting with the charge one.

### 3.3.1 Pseudo-Bump:

In our project, the pseudo bump serves as the initial point for the accumulation of kinetic energy. This bump is 3D printed using PLA filament and consists of several main sections:

Fixed Joint: this joint is fixed in place, allowing the bump to rotate around a specific axis by 25 degrees, which represents the maximum angle to ensure it does not disturb vehicles passing over it. The rotation of this joint transfers motion to the Bearing, which then passes it on to the rest of the system. [9]

Movable Joint: This is the highest point of the bump, with a height of 2 cm above ground level. When the bump is pressed by a passing vehicle, the triangular-shaped bump opens up and flattens to align with the road surface. The rotation of this joint increases the opening angle to achieve alignment with the ground.

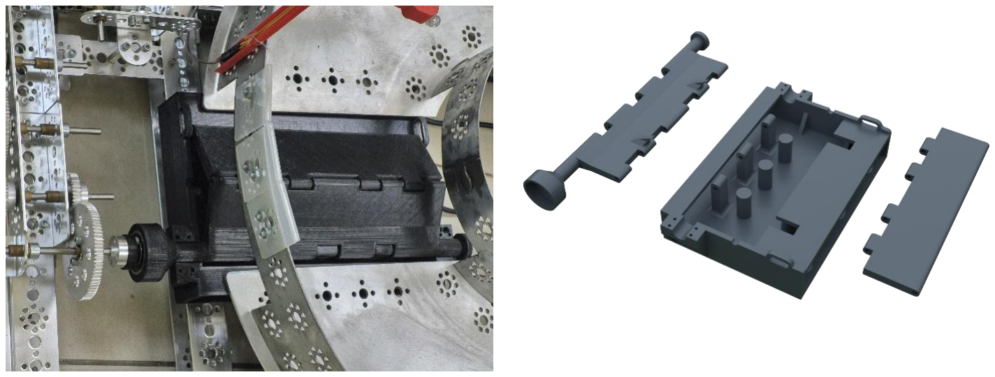
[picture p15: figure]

Springs: The springs compress when a vehicle presses down the bump. Once the pressure is relieved, the springs return to their original shape due to their elasticity, returning the bump back to its initial height.

### 3.3 MECHANISMS DESIGN

### Figure 3: Car Pseudo-Bump

To ensure that the pseudo-bump doesn ’t accumulate energy more than the system could store (maximum charge phase) we added a servo motor to flatten the bump (lock it to the ground level). our choice of the bump ’s angle and height value is suitable for the small-scaled prototype. These values ensure comfort pressing of the bump by the passing car (the small robot in our prototype) because of the low height (2 cm), while making sure not to reduce the amount of accumulated energy due to the large angle (25 degree) compared to standard bump designs in real life scales.

### 3.3.2 Motion Transmission and Torque Amplification Mechanism:

After gathering kinetic energy from the pseudo bump, the motion transfers to the second phase through three steps:

First Stage: A clutch or Bearing (one-way gear) prevents reverse motion in the system when the pseudo bump returns to its initial position (because of the springs) after being compressed, allowing the motion to be transmitted in only one rotational direction (the bearing used in the prototype) [10].

Second Stage: The motion then passes through a gearbox with a speed amplification ratio of 4.

Third Stage: This involves a worm gear that transmits motion in one direction (only towards the lifting system) and prevents reverse rotation and the falling of the mass, amplifying torque by a factor of 40. Thus, till this point, the torque of the lifting stage is increased by a factor of 20 (for more details, check the calculations here).

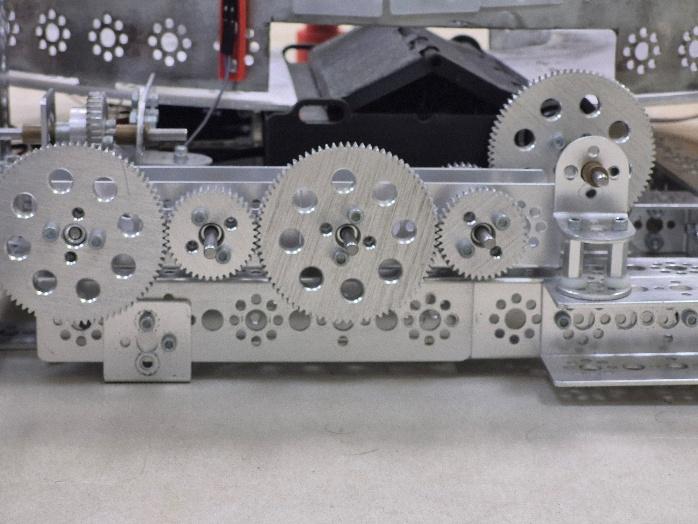
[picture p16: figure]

### 3.3.3 Lifting System:

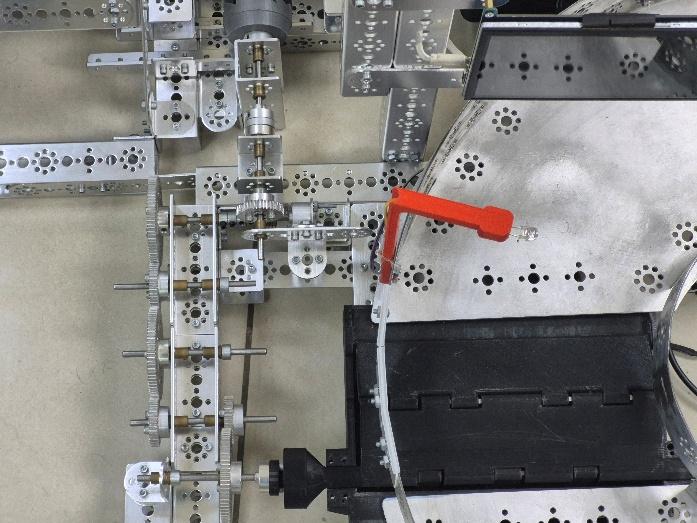
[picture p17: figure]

This is a pulley system that contains multiple pulleys responsible for the mass-raising operation. These pulleys are set as follows:

- Main Pulley (Spool): a pulley with a radius of 1.75 cm (for more details, check the calculations here), which in its turn amplifies the torque by its arm (1.75cm).
- Guiding Pulleys: Two guiding pulleys are located at the top of the tower. Their main function is to direct the rope along the correct path, ensuring that it stays properly aligned throughout the lifting process.

### Figure 4: Bump to Mass Gearbox

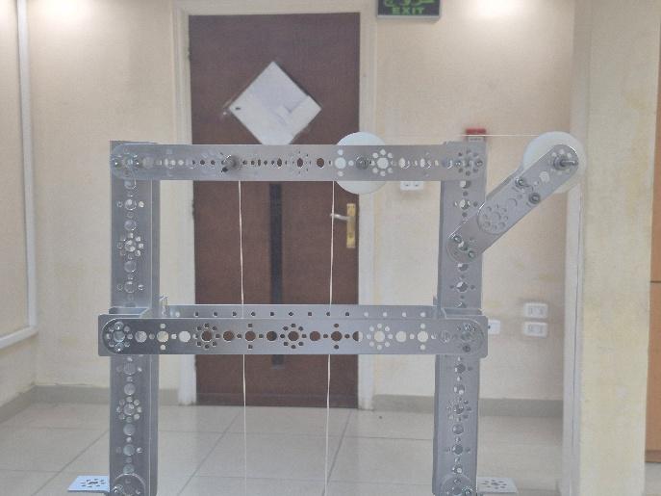
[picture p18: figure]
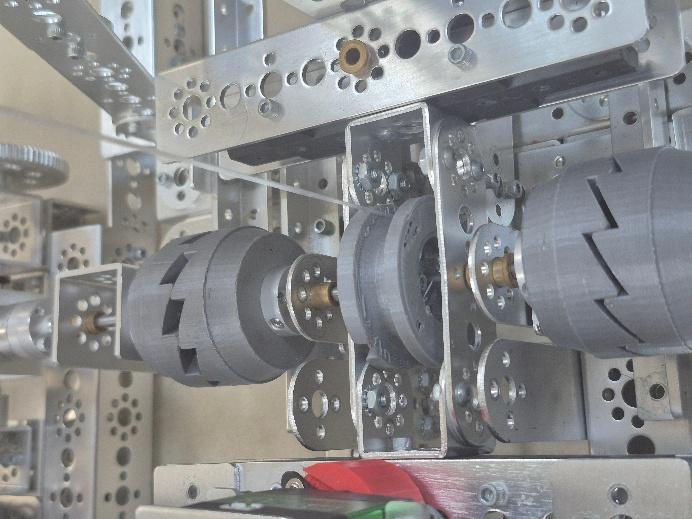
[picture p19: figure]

- Mass Pulley: Lastly, there is a pulley on the mass directly. This pulley serves many purposes: it protects the rope, increases the stability of the mass movement, and finally, multiplies the torque by a factor of 2 when raising the mass. This makes the overall torque amplification of the lifting process 20 (1/4 for the first stage * 40 from the worm gear * 2 from the mass pulley). This pulley plays a crucial role in our pulley system by adding these benefits and helping to reach the appropriate discharging time.

### 3.3.4 Connecting and Disconnecting Mechanism (C&D):

After the mass is raised to its highest point, the system stores energy to its full capacity. Now the system is in the maximum charge phase, and it should be locked (the pseudo-bump should be flattened). Then the system will be ready to discharge whenever the sunlight fades, which is determined by a light sensor. First of all, we need to disconnect the main pulley from the gearbox and connect it to the energy generation system (the motor and its own gearbox). Here comes the need for the connecting and disconnecting mechanism. The key component is a 3D-printed PLA parts shaped like a circular chainsaw tooth, designed to transfer energy in one direction. When the main pulley is pushed to the gearbox direction, two of these parts match and the gearbox transfers motion to the pulley, but when the pulley is pushed the other way, the parts in the gearbox side mismatch, and another two of these parts match so that the motion from the pulley is transferred to the motor side gearbox. To move the main pulley between these two phases, we used an HTS-35H Servo motor with a torque of 35KG/CM, connected with a rack and pinion mechanism to

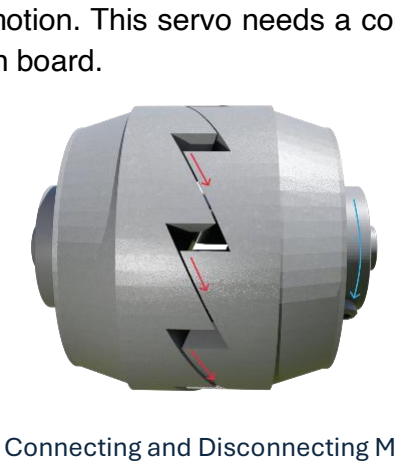
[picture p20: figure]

convert rotational motion into linear motion. This servo needs a controller that consists of an ESP32 core board and a multi-functional extension board.

Figure 5: Main Spool | Figure 6: Guiding Pullies

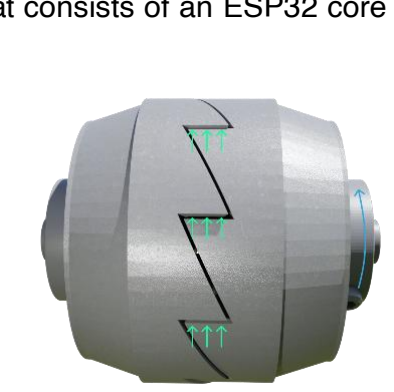
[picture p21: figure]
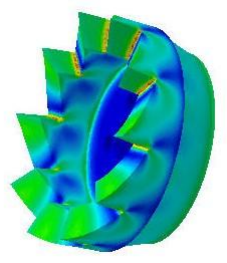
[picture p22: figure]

### Figure 7: Connecting and Disconnecting Mechanism

### 3.3.5 Motor Gearbox:

Because of the high weight of the mass that could be utilized, and in order to increase the discharge time of our prototype, the generator is not connected directly to the main pulley, which rotates due to the fall of the mass. There is a speed amplification factor formed by the pulley on the mass increasing the speed (on the generator ’s side) by two, and a gearbox between the motor and the main pulley with speed amplification factor of 1.5, 3 in total (for more details, check the calculations here).

### 3.3.6 Electrical Circuit & Load Management:

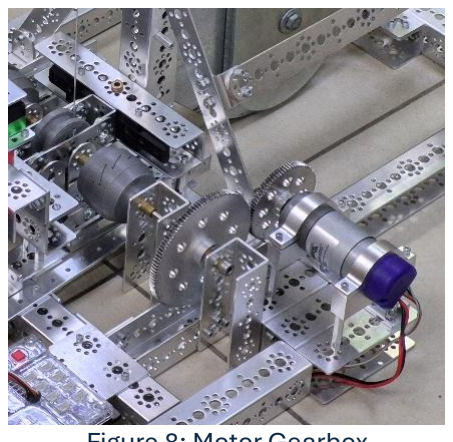
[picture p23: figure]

The main electrical load in our prototype consists of 6 white 0.5-watt 8 mm LEDs powered by the energy from the falling mass during discharging. The motor generates around 6 V. To make it suitable for lighting the LEDs, we use a step-down converter regulating the voltage at 3.3 V. To manage the increasing voltage caused by the accelerating mass, we use an automated system with an ESP32 controller (the same ESP we used for C&D servo), relay board, and sensors like the encoder of the TorqueNADO motor. This system adds an extra load, a fan (DC Motor) with another DC Motor Controlled by BTS motor driver driven by a pwm signal, which converts excess voltage (extra speed) to a beneficial use. The total discharge time is about 35 seconds. The full schematic diagram is shown in figure 24 in appendix 2.

### 3.3.7 Field Design:

The field is the part of our prototype that is supposed to represent the
road with cars on it, to present how our idea will work in real life, we made a circular path for the road, with a car to represent the traffic, the path contains walls on the sides with a distance of 17 cm between them (the width of the path), and a determined place to put the pseudo bump. The car has a shape of 18 x 16 cm² and a room on its top to provide the ability for modifying the weight of the car. The car drives on the path blocked by the walls on both sides, with a simple manner of going forward, relying on the smooth rotation of the walls to turn and run in the circular path.

### Figure 8: Motor Gearbox

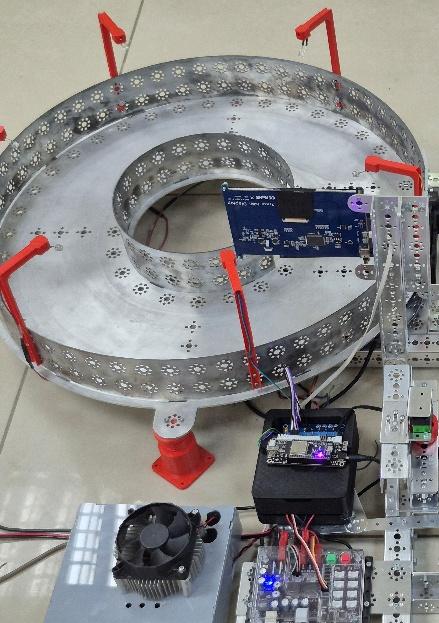
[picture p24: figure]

### Figure 9: Field Design

### 3.3.8 Tower Design:

Given the weight of the mass in our prototype and the required lifting height, we designed a compact, efficient tower. After testing various designs and making improvements based on engineering concepts, we arrived at the final structure, capable of steadily supporting the mass. The tower stands 120 cm tall, with a functional height of 105 cm. It is built entirely from Tetrix Kit parts, using channels, flat pieces, and L brackets. The tower consists of two main columns that hold the mass (which helps stabilize the structure). A strong and fixed base supports the weight and is designed for easy maintenance and assembly. Our studies indicate the need for a mass of approximately 11.2 KG (for more details, check the calculations here); its two ends are blocked from the sides by the channels of the tower ’s columns, so that the mass fits in place. This gives us more control over the mass descent.

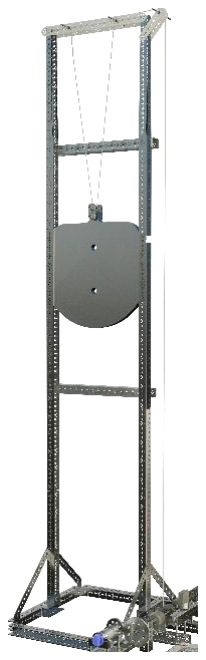
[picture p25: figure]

Calculating the weight of the mass needed was done using these equations, knowing the
height of the tower and the power requirements to ensure the demo reaches a runtime of 35 seconds:

η ⋅ E{mecℎ} = E{elec}
(1)

## ⇒ m ⋅ g ⋅ ℎ = Pload ⋅ t ⋅

1
η

(2)

⇒ m =

Pload⋅t
η⋅g⋅ℎ

(3)

SYMBOL | DESCRIPTION
E{mech} | Mechanical Potential Energy (Joules)
E{elec} | Electrical Energy (Joules)
Pload | Electrical Load (Watt)
η | Efficiency Factor
m | Calculated Mass (kilograms)
g | Gravitational Acceleration Constant (m/s

2
)
h | Efficient Height of the Tower (meters)
t | Operating Time (seconds)

### Figure 10: Tower Design

### Table 1: Energy Calculation and their Definitions

### 3.3.9 Prototype Scaling and Dynamic Calculations:

Equations (4) and (6) represent the final differential equations of the current in the generator and load circuit, describing their dynamic behavior. By modeling these equations, we determined the optimal system parameters, including the mass, motor gearbox ratio, and the radius of the main pulley. Moreover, by considering the angle of the speed bump and the length of its arm (specified in the bump section), we derived the torque amplification ratio required to be applied to the main gearbox to effectively lift the mass by the car.

i′

̇ =

kω−(Rm+Rl

)i
Lm+Ll

(4)

Ieq = Im + Igears +

Imass+Ipulley
K1

2

(5)

ki −

mg
K1

## = (Ieq +

mr
K1
2 ) θ̈ | (6)
SYMBOL | DESCRIPTION
i̇ | Motor Current
r | Radius of the Spool (Main Pulley)
θ̈ | Angular Acceleration of the Motor Shaft

i′

̇ | Rate of change of current
ω = θ̇ | Angular speed of the motor shaft
k | Back EMF constant of the motor
Rm | Internal resistance of the motor
Rl | Load resistance
Lm | Inductance of the Motor
Ll
| Inductance of the Load
Ieq | Equivalent moment of inertia of the system
Im | Moment of inertia of the motor
Igears | Moment of inertia of the gearbox
Imass | Equivalent inertia of the lifted mass
Ipulley | Moment of inertia of the pulley
K1 | Motor gearbox ratio
m | Calculated Mass (kilograms)
g | Gravitational Acceleration Constant (m/s
| 2
)

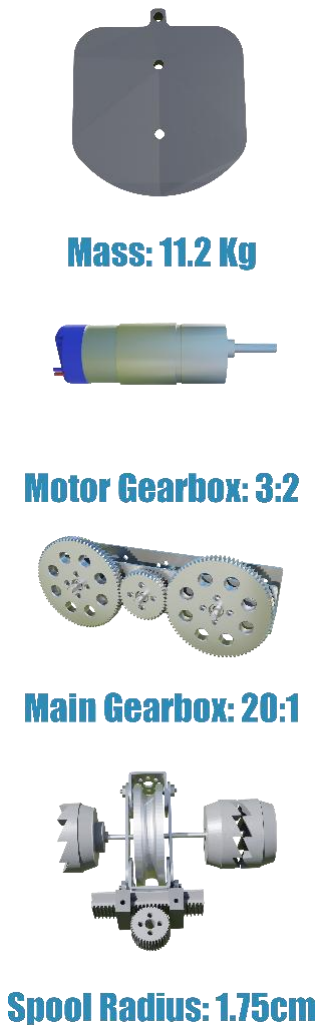
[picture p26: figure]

### Figure 11: Final Results

### Table 2: Dynamics Calculation and their Definitions

### 3.4.1 System Logic and ROS Integration:

The control logic of our project is based on a state-driven system that manages all operations automatically. The code defines several modes that represent the system ’s different working states, such as charging, discharging, and fast charging. Each mode activates specific components and deactivates others to ensure smooth transitions and prevent conflicts between actions.

The operation of our project is based on ROS, which facilitates the
communication between the system components and the management of the overall process. We used a raspberrypi 4 model B device as the brain of our system, on this device the ROS Master runs and the other controllers connect to it via Serial or Wi-Fi. There are four nodes communicating with each other to dictate the behavior of the system by setting its state to a specific Mode. The modes are:

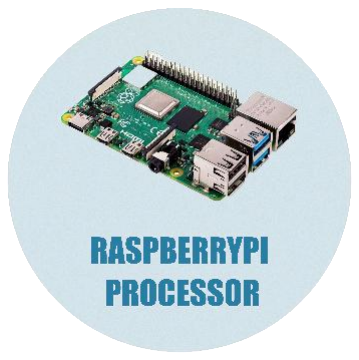
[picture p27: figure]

- Charging: By connecting the C&D (Connecting and Disconnecting)
mechanism to the gearbox and activating the pseudo-bump, this mode is
called Charging because the mass is raised by passing cars and the system is charging.
- Discharging: By connecting the C&D mechanism to the motor, and deactivating the pseudo-bump, the system enters the discharging mode.
- Fast Charge: This mode is designed only for the prototype. To clearly present the demo, we needed a way to lift the mass quickly. Therefore, the Fast Charge mode was added to lift the mass using the motor. It is activated by connecting the C&D mechanism to the motor and powering the motor to lift the mass and charge the system.

The ROS nodes responsible for activating the various modes:

1) Python Node (Main Control):

The Python code serves as the main node in the system. It organizes the distribution of commands to the other nodes and handles workflow cases. This node changes the current mode of the system based on sensor readings or commands from the web page node (system dashboard) by publishing the mode to the ESP - Servo node and the PRIZM controller node. The Python node ensures that the operating of all system components is integrated and synchronized.

2) Web Interface Node:

A user-friendly web page that is an essential component for tracking the system values and controlling it. The interface displays the motor voltage and encoder position in real time. It also shows when a car passes over the pseudo-bump. The system can be controlled from the interface through buttons designated to set the different modes. For example, when the Charge button is clicked, the interface node sends a service request to the python node to change the mode being published to Charge. For implementing It, we used the rosnodejs JavaScript library so that it connects locally with the ROS master. We associated an IP address and a port to make it reachable from other devices.

### 3.4 CODING OF THE SOLUTION

### Figure 12: Raspberrypi

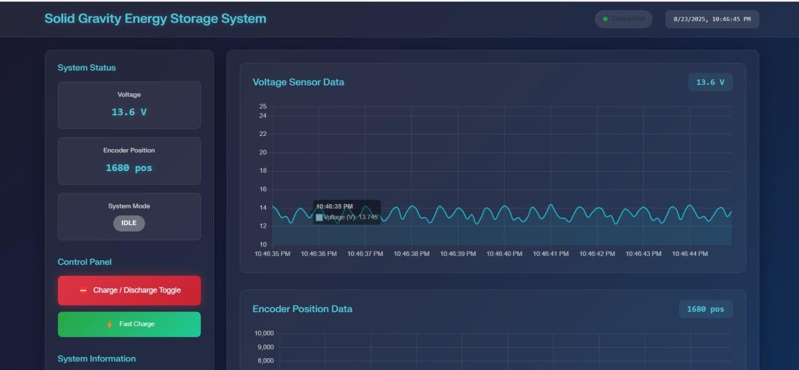
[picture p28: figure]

3) PRIZM Controller Node:

The PRIZM controller contains a part of the Arduino code, which reads the values of some sensors and controls the motor and servo motor responsible for the pseudo-bump state (activated or deactivated). This code continuously publishes the readings of the encoder and the voltage values, so that this information can be used in the other nodes. It reads the mode value published by the python node and act accordingly. In addition to determining whether it is

night or day using a light sensor and sending this value to the main control node to choose the appropriate mode for the system.

4) ESP Node:

The HTS-35H Servo motor we used for the stability of the C&D mechanism needs control from an ESP32 controller. This board contains another part of our Arduino code that controls the C&D Servo beside the relay to supply the load in the discharging mode. This node publishes when a car passes over the pseudo-bump by reading values from its limit switch. It also reads the mode

value published by the Python node and acts accordingly. One more, it controls the pwm signal sent to the BTS driver to control the overload.

You can explore our GitHub repository by pressing this link here, (https://github.com/salmandaher/VLNs_Team_GraviPower) or pressing on (https://github.com/salmandaher/VLNs_Team_GraviPower)

the following icon to get more details about the packages and the codes.

### Figure 13: Web Dashboard of the System

### Figure 14: PRIZM Controller

### Figure 15: ESP32 Sheild

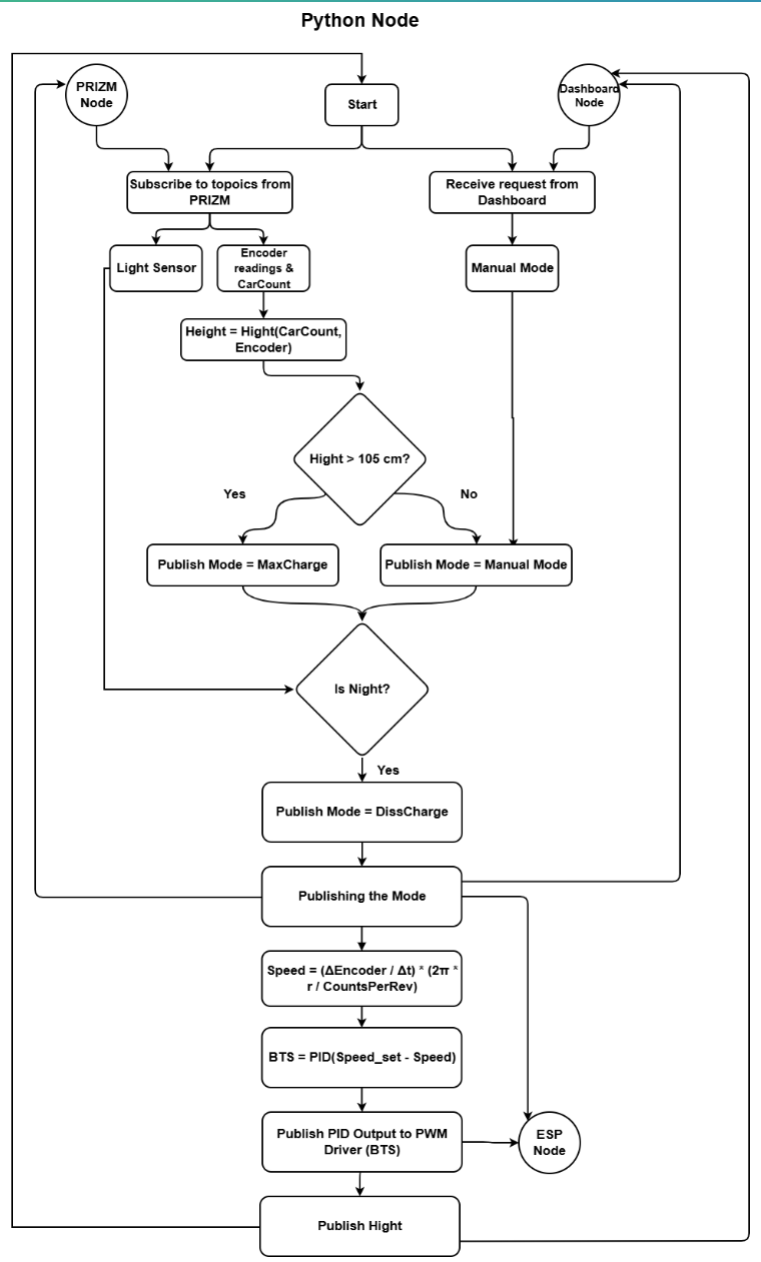
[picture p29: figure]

### Figure 16: Flow works of the Main Control Node

### 3.4.2 PID Control Algorithm:

For the control algorithm, we have a variable additional load on the generator (represented by two DC motors). The power allowed to reach this excess load is controlled by a BTS motor driver using the PWM pin. In the Python node, we use the encoder readings and apply a PID algorithm to keep the mass descending speed at the right point on the efficiency graph (6V operating voltage) [13] , thus generating electricity with the maximum efficiency possible. The Python node calculates a value between 0–255 and sends it to the ESP node, which adjusts the PWM value on the BTS.

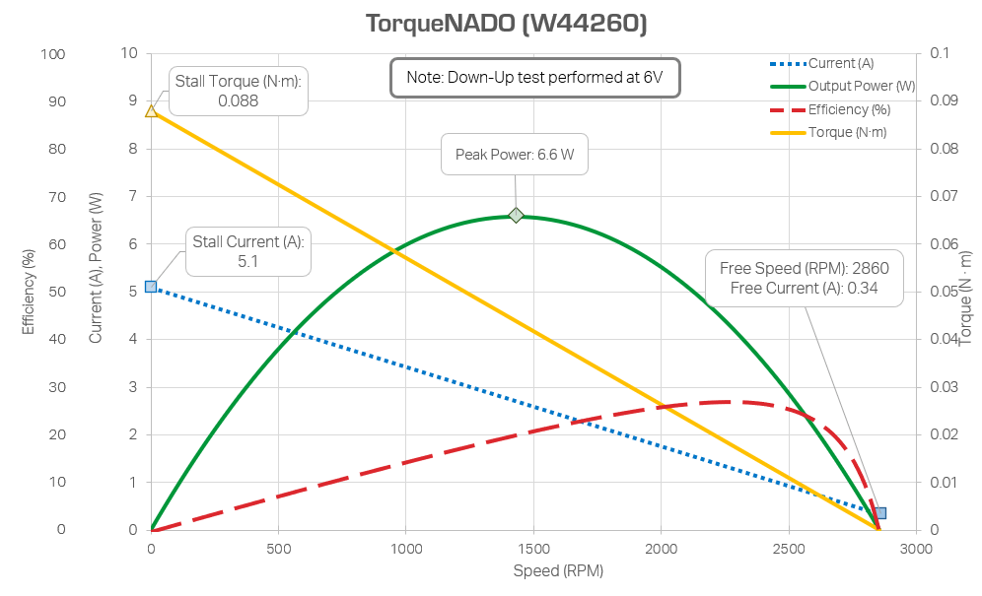
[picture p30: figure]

### Figure 17: TorqueNado Motor Efficiency Diagram

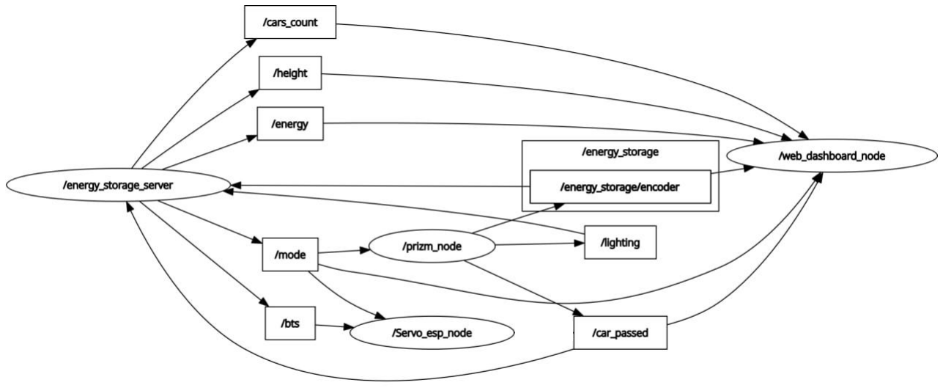
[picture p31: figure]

### Figure 18: RQT Graph showing how different ROS nodes of the system are connected

- Challenges during tower construction:

The first version of the tower was somehow steady, but to increase its stability according to engineering concepts, we removed the straight beams that connect every two adjacent channels and replaced them with triangular connections, to increase stability and efficiency [11]. It seemed to work well at first, but we faced some problems with sitting it without tilting, it also costs too many Tetrix parts, which made us think of a solution for this problem leading us again to the third and final version of the tower, having a strong base to correct tilting, and high efficiency using fewer Tetrix parts, the final version met our requirements perfectly. Images of the different versions are included on our GitHub repository.

- Challenges during developing the Disconnecting and Connecting Mechanism:

The connecting and disconnecting process carries a significant risk, because it involves moving the main pulley while the mass is hanging in the air. This process needs to be swift and precise to ensure the matching of the couplers safely, which caused us to face many challenges to reach the current stable mechanism. At first, we used a stepper motor. The problem we faced with it was that the motor has quite a high torque but a low speed. For this process, we need both high speed and torque to guarantee safety and efficiency, so we implemented another method: we used a servo motor with a torque of 35 kg/cm. The new powerful servo was able to safely lock the mechanism to a fixed position. It also had enough speed to switch the position correctly and smoothly.

- Challenges with 3D-printed parts:
In the first pulleys we printed, we faced a challenge. When the pulley was used many times, it started to crack and break eventually, because of the tension caused by the weight of the mass. This problem is caused by the 3D printer setting; we had to test many models to reach the most efficient infill and thickness. Also, some parts, like the C&D coupler, faced a problem with the smoothness of the edges, which caused issues in the mechanism. Thus, we tested many models of each 3D printed part to find the most efficient version of each, and to determine how to choose the settings of the printer.

### 3.5 CHALLENGES DURING DEVELOPMENT PROCESS

Modern cities consume huge amounts of energy every day, while the demand for cleaner and more reliable power continues to rise. However, many renewable energy sources such as solar and wind are intermittent. They depend on weather, making energy storage a critical challenge. Traditional batteries, although widely used, are expensive to maintain, have limited lifespans, and create environmental and disposal problems. At the same time, cities are full of constant movement - especially road traffic - which produces mechanical energy that is completely wasted. Our project addresses both issues by capturing a portion of this everyday mechanical motion and storing it as gravitational potential energy, which can later be released as electrical power when needed. This approach provides a sustainable, low-maintenance, and long-life alternative to chemical batteries, using a system that can be integrated directly into urban infrastructure and scaled to support community-level energy needs.

- Enables energy independence for large companies by allowing them to generate and store their daily energy needs.
- Environmentally friendly, reducing pollution and emissions compared to traditional storage methods.
- While individuals or small entities may not directly use the pseudo bumps due to installation challenges, they can benefit from the storage system in different sizes for various uses.
- This project directly contributes to global sustainability efforts, particularly SDG 7, SDG 9, SDG 11, and SDG 13, by enabling cities to generate and store clean energy using their own everyday motion.

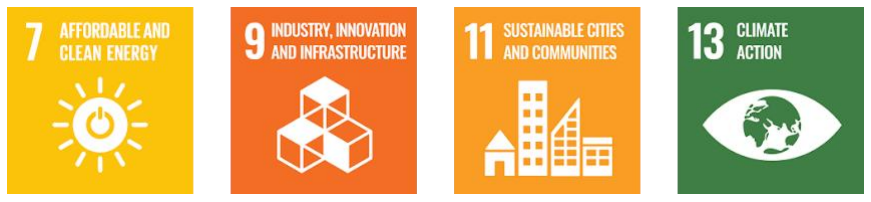
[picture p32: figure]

We studied a case where we can light the city center (Homs City - Syria) as a concrete example of our prototype. We first Scheduled a meeting with Homs City Traffic Department Manager Eng. Bashar Alsebaai, we discussed the possibility of scaling our prototype to a real-world project where we can benefit the city. He was very excited about the project and provided us with needed data for calculating and designing the bigger-scale project.

# SOCIAL IMPACT AND INNOVATION

### 4.1 THE NEED FOR OUR PROJECT

### 4.2 ON-GROUND EFFECTS OF THE PROJECT

### 4.3 CONCRETE (REAL-WORLD) EXAMPLE

### Figure 19: Sustainable Development Goals our Project Covers

This map shows the real place where we chose to light the streets:

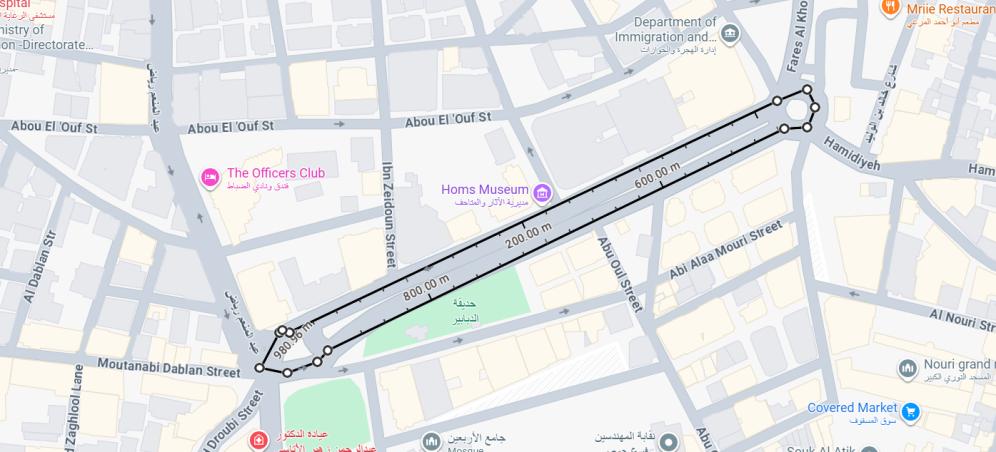
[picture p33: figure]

Table 3 shows the estimations we built [12]:

Item | Estimation | Notes
Distance of Lightening (m) | 850
Number of LEDs | 17 | According to spacing distance
| | (50 m) according to Syrian code
Power of each LED (Watt) | 40 | link (https://seminglighting.com/Products/SM-40-LED-Street-Light-1117.html)
Lighting Time (hours) | 6
Traffic Density (Cars/day) | 15000 | According to the City Police
| | Command Cente
Average Car Weight (ton) | 1.3 | According to the most owned
| | cars in Syria
Tower Height (m) | 20
Mass Needed (ton) | 75
Torque Amplification (Bump/Mass) | 144
Vertical Displacement of Mass (Cycle/m) | 0.0013
Cable Diameter (mm) | 22 | link (https://www.alibaba.com/product-detail/Manufacture-Rope-Wire-11mm-Steel-Cable_1954495652.html) The load is divided by 2 due
| | to the pulley system design
Cable Length (m) | 80
Cable Cost ($) | 56 | link (https://www.alibaba.com/product-detail/Manufacture-Rope-Wire-11mm-Steel-Cable_1954495652.html)
Gearbox Cost ($) | 268 | link (https://www.indiantradebird.com/product/gearbox)
Mass & Tower Cost ($) | 4000
Total Cost ($) | ~9000 | Elements costs + Installation
| | Costs

### Figure 20: Main Road Chosen for the Study

### Table 3: Estimations for the Case Study

To bring this solution into real urban environments, collaboration with key partners is essential. Municipal authorities and city planning departments are needed to integrate the system into streets and public spaces, ensuring safety and compliance with road infrastructure standards. Energy distribution agencies and local utility companies are important partners to connect the generated power to the lighting network and manage stored energy release. Engineering and manufacturing partners can support the production of durable mechanical components at scale. In addition, universities and research centers can assist in continuous improvement, data monitoring, and system optimization. By working with these partners, the project can move efficiently from prototype to full deployment, ensuring technical reliability, economic feasibility, and long-term positive impact on the city.

Choosing the best place to install our system is a comprehensive process, as it requires careful evaluation of efficiency, benefits, and long-term impact. To solve this issue, we developed an AI tool that analyzes data using some parameters (traffic density (30% weight), infrastructure (20% weight), and population density (25% weight) These weights reflect the importance of each factor) and rates all suitable places in the city. The AI model combines data from: traffic and transport agencies for traffic density, OpenStreetMap, and municipal GIS layers for infrastructure, and census and demographic databases for population. In addition to that, we implemented this model into a web page, we used a Random Forest Regressor model. The model is trained on a composite score that combines these factors with defined weights. so, the user can choose a city, and the model will show a comparison between the suitable place and their rate, and pin the locations on a map, so the user will be able to detect the address. Also, the user can adjust the classification setting based on the importance of each parameter.

### 4.4 EXTRA ELEMENT OF ENTREPRENEURSHIP - PARTNERS

### 4.5 AI MODEL OF GRAVIPOWER

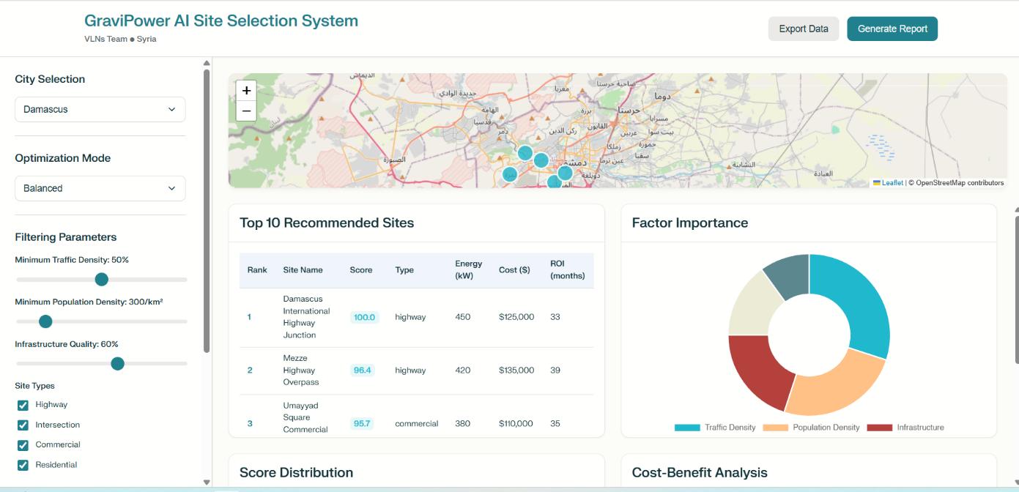
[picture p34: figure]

### Figure 21: GraviPower AI Site Detector

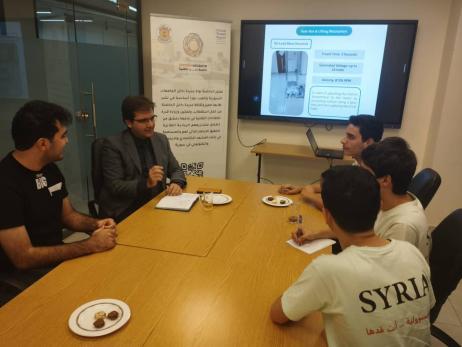
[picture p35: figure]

The next step for our project is expanding usability to individuals. While currently focused on large companies and governments, we aim to offer residential versions of our system. Homeowners could integrate a storage-only system with renewable sources like solar panels, using solar power to lift the mass for energy storage. This expands access and promotes clean energy use.

We had the chance to meet the Founder & Manager of EvoTech Incubator in Syria, Damascus Dr. Ghaith Workozek who helped us figuring out the aspects of adapting the project and upscaling it. Dr. Workozek showed his acceptance for the project, and he said
that he liked the idea. After presenting our project, we met some
business experts in the incubator, and there we presented our
study for Homs city center and they provided us with the important sheets to make a full business.

We also discussed following a Lean Startup roadmap to move from prototype to deployment as follows:

Our project offers a groundbreaking approach to energy storage by using the potential energy of a suspended mass. Unlike traditional systems, we maximize energy efficiency by precisely controlling the mass ’s descent without relying on brakes, minimizing friction and heat loss. Smart controllers manage the electrical load to optimize energy generation, making the system more sustainable and efficient. To add, our energy accumulation mechanisms are purely mechanical; that means more efficiency at power transfer.

Additionally, we harness kinetic energy from everyday activities, like cars driving over bumps, and can adapt the system to other sources like waves or wind, providing flexible and innovative clean energy solutions.

Our project focuses on developing an innovative energy storage system using gravity, where we harness the kinetic energy generated by vehicles. This clean and renewable system converts the mechanical energy produced by cars into stored potential energy, which is used then to generate electricity when needed. What makes our system unique is its high efficiency and innovative method of energy retrieval. We control the speed of the descending mass to generate as much energy as possible, without relying on traditional brakes that waste energy, our project will significantly impact by providing sustainable energy storage solutions for large companies, especially in areas with heavy traffic. Our system also offers the potential for energy independence and environmental benefits by reducing reliance on traditional energy storage methods that harm the environment. We aim to expand our project to include harnessing other energy sources like wind and wave motion, making the system more versatile and effective in different regions.

## And that is our: GRAVIPOWER STORED BY THE HOUR

### 4.5 STARTUP IDEA - NEXT STEPS & PROTOTYPE DEVELOPMENT

### Figure 22: Meeting with the head of EvoTech Incubator Dr. Workozek

### 4.6 KEY INNOVATION

# CONCLUSION

### Figure 23: Time Plan for the Deployment of the Project

[1] K. Chen, “Types, applications and future developments of gravity energy,” MSMEE, 2022.
[2] J. D. Hunter, “Underground Gravity Energy Storage: A Solution for, ” MDPI, 2023.
[3] W. Tong, “Solid Gravity Energy Storage: A review, ” North China Researchgate, July 2022.
[4] “How To Read DC Motor & Gear Motor Performance Curves,” lsproducts, 2024. [Online]. Available: https://lsproducts.com/design-note/how-to-read-dc-motor-gear-motorperformance-curves/
[5] D. R. Gupta, “Gravity Based Energy Storage System: A Technological Review,” ISSN, 2020.
[6] A. C. Ruoco, “Storage Gravitational Energy for Small Scale Industrial and Residential Applications,”MDPI, 2019.
[7] M. H.-E. Haider, “ Analysis of Speed Breaker Mechanism for More Effective Electricity Generation, ”ResearchGate, 2015.
[8] E. E. P. special, “Why speed of the induction motor decreases with an increase in load? — Effect of

loading on I.M.,” YouTube, Jan. 1, 2023. [Online]. Available: https://youtu.be/jshQqLYmIPw?si=

SwQvD8aXgKFG_UD.

[9] S. Ibrahim and M. El-Gindy, “Dynamic Characteristics of Vehicles Passing Over Speed Humps,”International Journal of Vehicle Systems Modelling and Testing, vol. 5, no. 1, pp. 18–35, 2010.
[10] “CSK12PP One Way Clutch Bearing 12x32x10mm,” bearingstreet, 2024. [Online]. Available: https:

//bearingstreet.com/csk12pp-one-way-clutch-bearing-12x32x10mm/

[11] | “Running | a | Brushed | DC | Motor | as | a | Generator,” | Portescap, | 2021. | [Online].
Available:https://www.portescap.com/en/newsroom/whitepapers/2021/12/running-a-brusheddc-motor-as-a-generator
[12] M. Zeeshan, “Exploring the Strongest Structural Material Shapes in Building Construction, ” Alsyedconstruction, 2024. [Online]. Available: https://alsyedconstruction.com/exploring-thestrongest-structural-material-shapes-in-building-construction/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 (https://alsyedconstruction.com/exploring-thestrongest-structural-material-shapes-in-building-construction/)
[13] [Online]. Available: https://motors.vex.com/other-motors/torquenado

### Organizations that helped us:

# LIST OF RESOURCES

# APPENDIX

21

Key Partners

Suppliers | of | sensors,
controllers, DC motors, and batteries.

Infrastructure companies.

Local | academic | and
research collaborators for technical expertise and
innovation.
| Key Activities System installation and maintenance at client sites. Demonstrating system capabilities and performance. Ongoing calibration and optimization of energy capture and storage mechanisms. Developing, updating, and monitoring system software and web interface. Technical support and troubleshooting. | | Customer Relationships Product website for easy communication and support. Troubleshooting guides for common issues. Direct contact with specialized support teams for assistance and maintenance
| Key Resources Technical equipment: DC motors, pulleys, ropes, sensors, controllers. Specialized infrastructure: Car bumps, gear systems. Skilled team: Mechanical, coding, and circuit design expertise. Digital tools: Web interface and ROS-based software for system monitoring and control. | | Channels Direct sales through the team's headquarters and communication lines. Demonstrations at industry and technology events to showcase the system. Networking and collaboration with energy companies and local government bodies for deployments.
Cost Structure Monitoring and software maintenance expenses. Construction costs including tower building=4000$, installation of pseudo-bumps, and infrastructure=324$. The total cost = 8648$ | | Revenue Streams Asset sales: Selling the energy storage system hardware and maintenance tools. Energy sales: Income from electricity generated Service contracts: Recurring fees from customers Total revenue = 721$ annual

Value Propositions

Providing sustainable, low-carbon energy solutions to communities and businesses. Enabling energy independence by allowing entities to generate and store electricity using clean energy sources.
Delivering large-scale energy capacity based on vehicle traffic density.

Customer Segments

Factories and large businesses seeking energy independence and cost savings.
Organizations focused on reducing carbon footprints, including companies and non-profits.
High-traffic centers such as transport hubs, parking facilities, toll booths, and highways.

# Appendix 1: Business Model Canvas

### Table 4: Business Model Canvas of GraviPower

# Appendix 2: Full Schematic of the Circuit

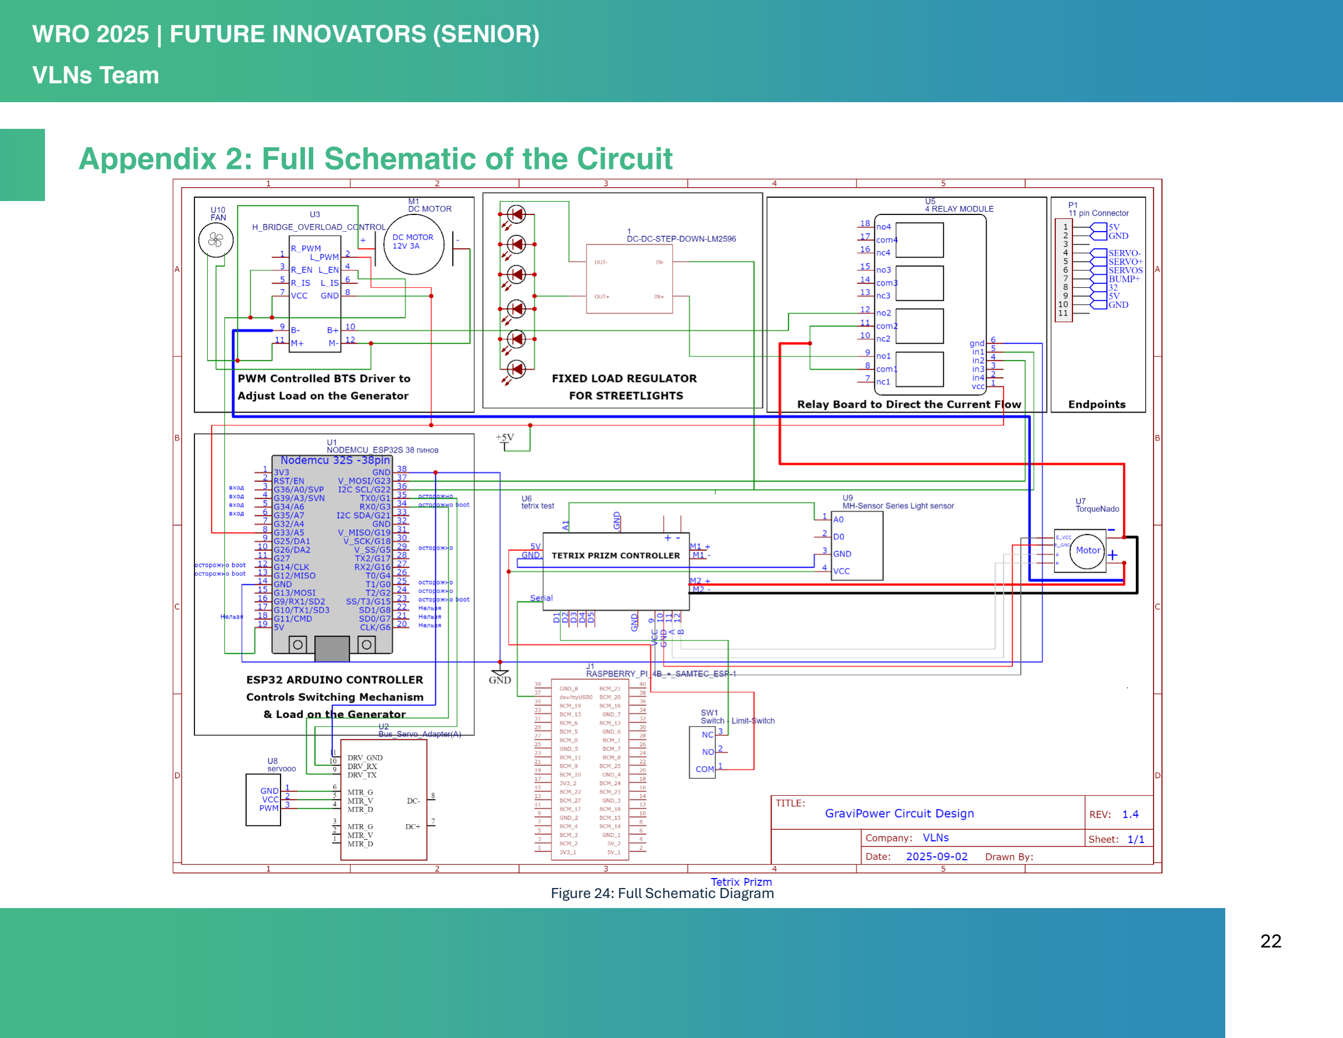
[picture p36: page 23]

22

### Figure 24: Full Schematic Diagram

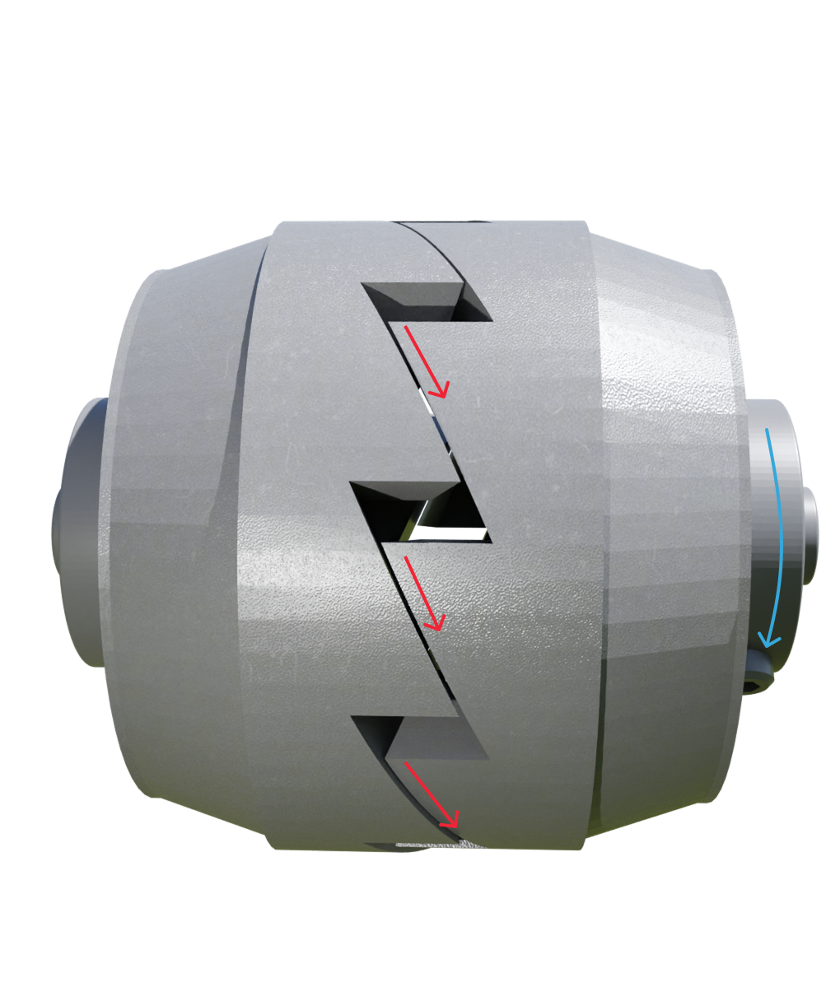
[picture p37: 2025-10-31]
imgs/C&D Disconnecting.png

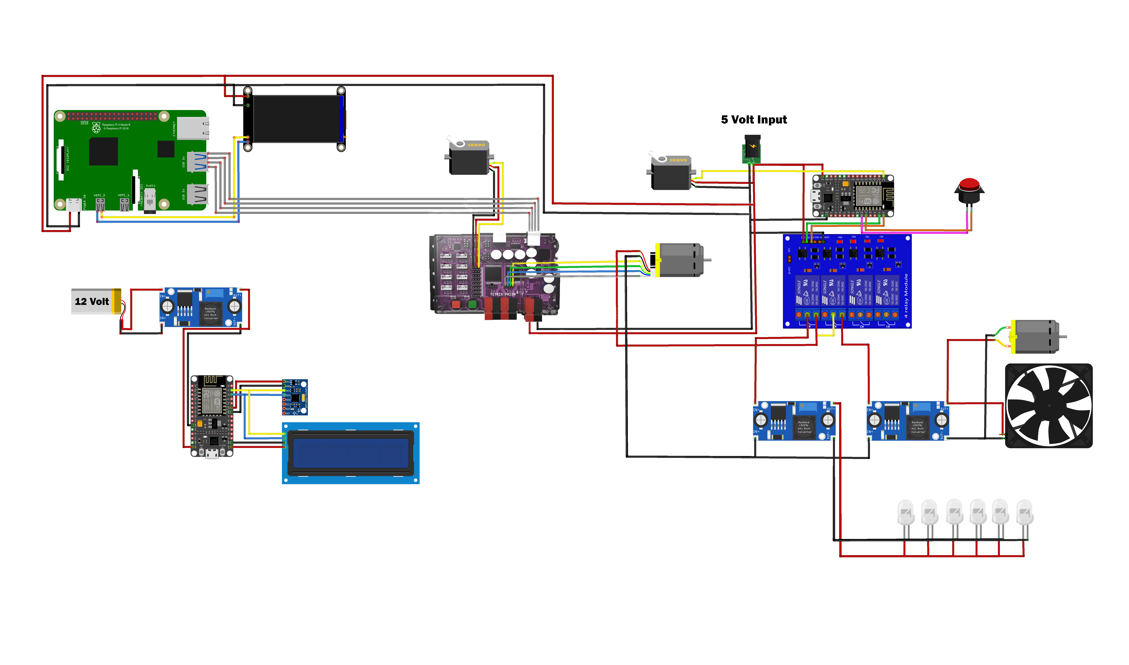
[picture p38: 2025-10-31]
imgs/Circuit .jpg

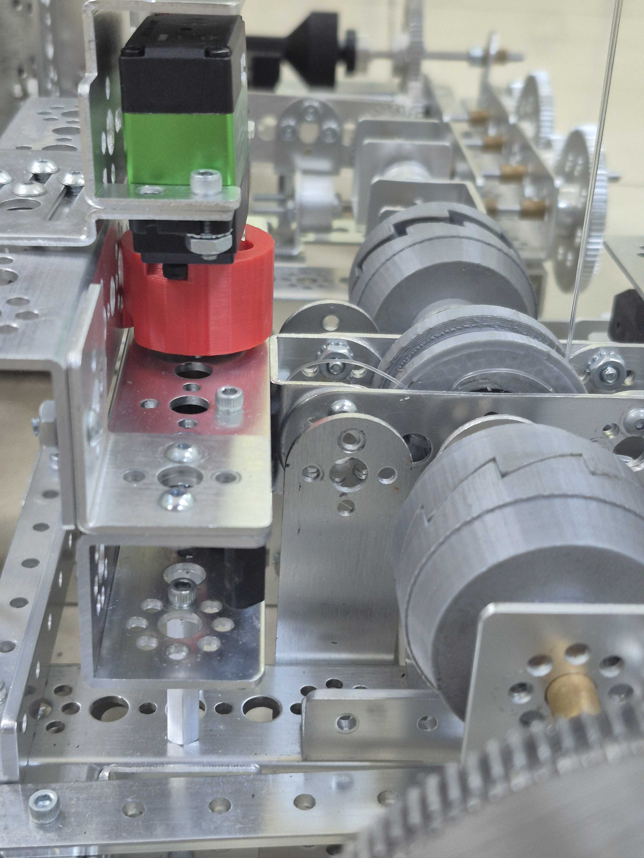
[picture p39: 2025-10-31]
imgs/project images/c&d.jpg

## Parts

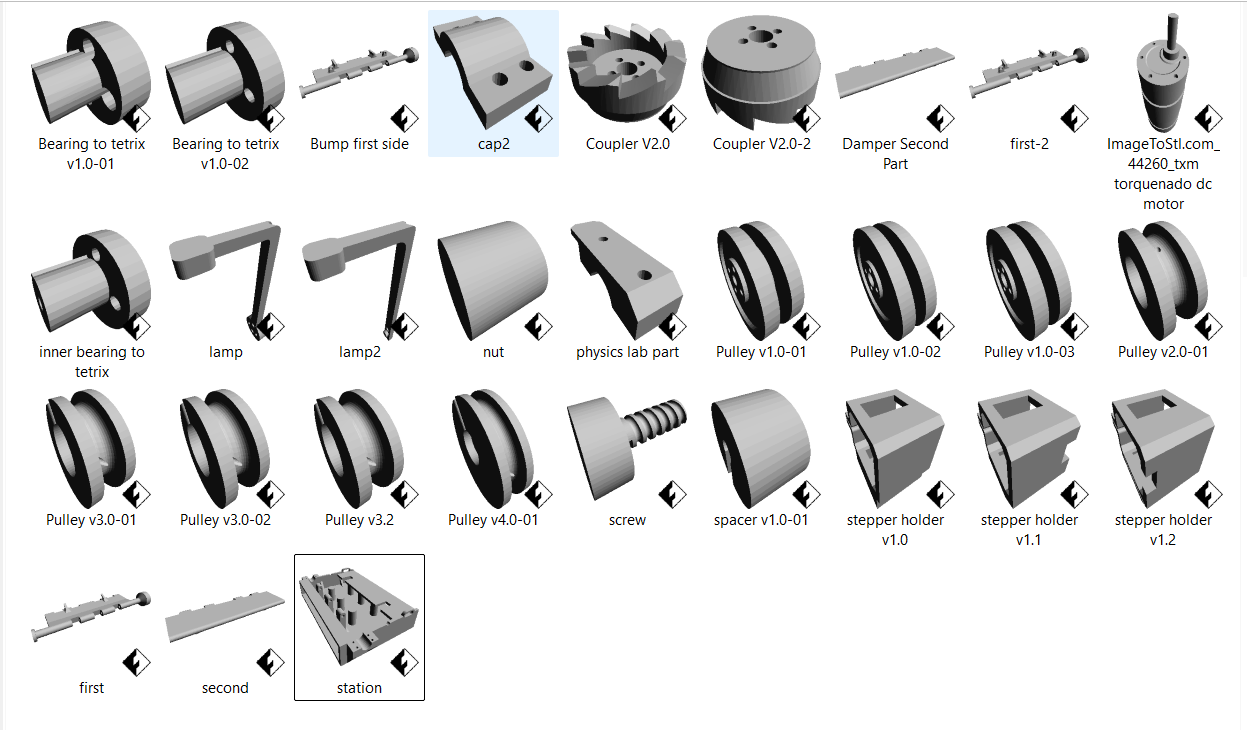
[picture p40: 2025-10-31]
imgs/project images/all 3d parts.png

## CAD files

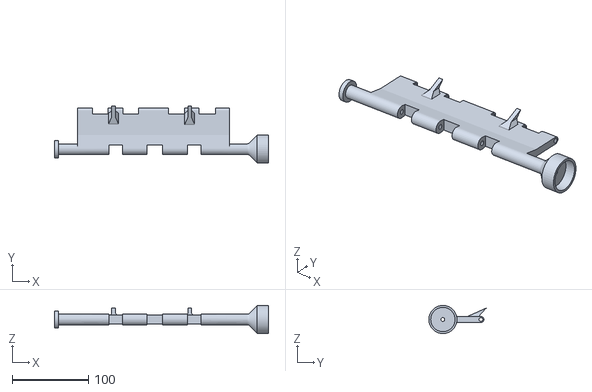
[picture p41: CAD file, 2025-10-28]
3d designs/stls/first.stl
281.0 x 75.4 x 37.0

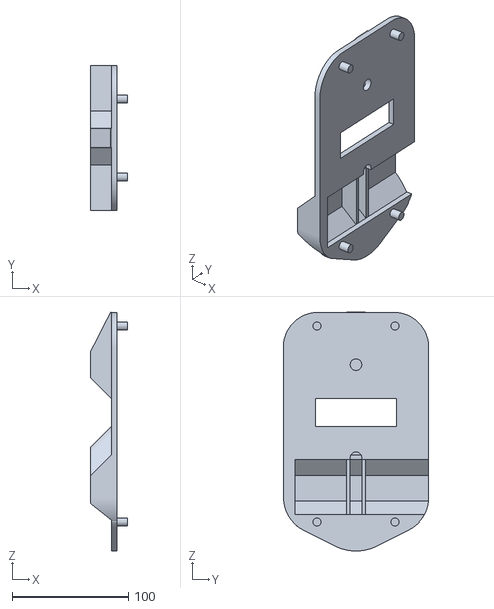
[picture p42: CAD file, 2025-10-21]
3d designs/stls/sensing unit/sensing_unit_v1.0 - 2.stl
32.0 x 125.0 x 205.5

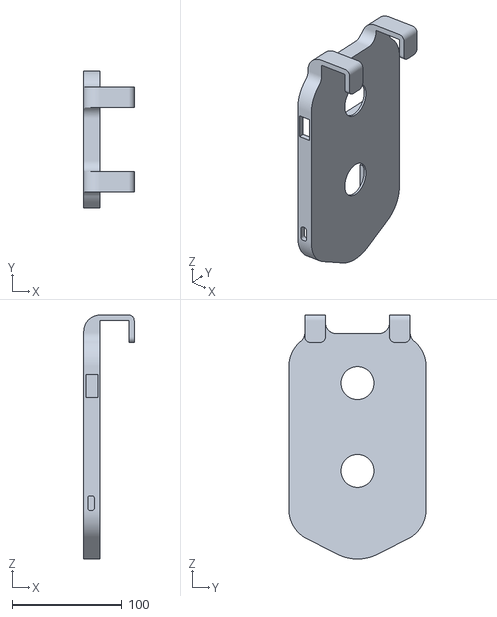
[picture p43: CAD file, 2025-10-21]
3d designs/stls/sensing unit/sensing_unit_v1.0 - 1.stl
46.0 x 125.0 x 222.2

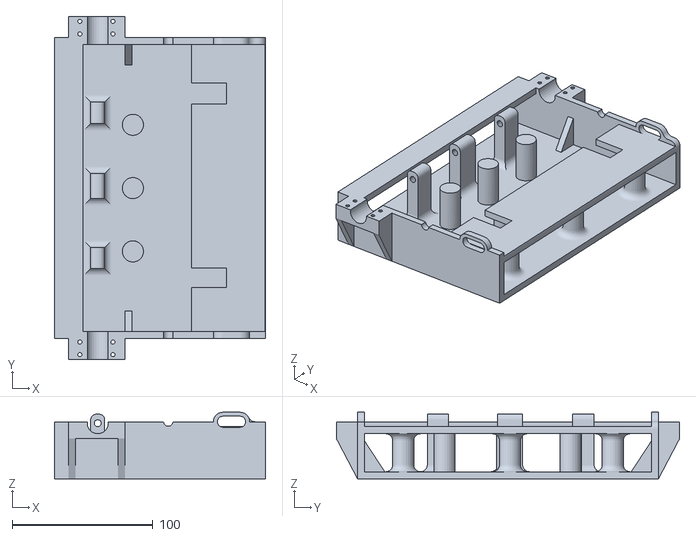
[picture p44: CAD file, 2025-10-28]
3d designs/stls/station.stl
150.0 x 244.0 x 47.4

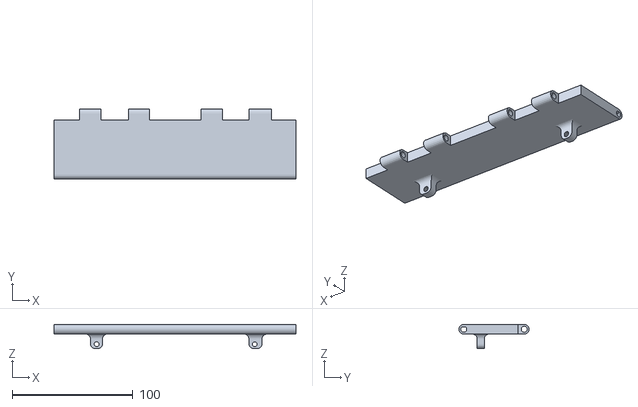
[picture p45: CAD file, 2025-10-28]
3d designs/stls/second.stl
200.0 x 58.0 x 20.0

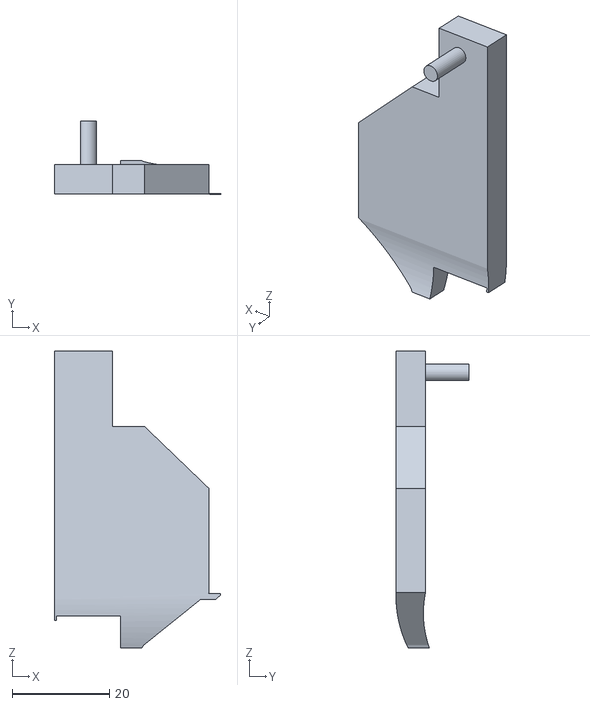
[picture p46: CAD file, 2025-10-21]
3d designs/stls/sensing unit/sensing_unit_v1.0 - 3.stl
34.1 x 15.0 x 61.0

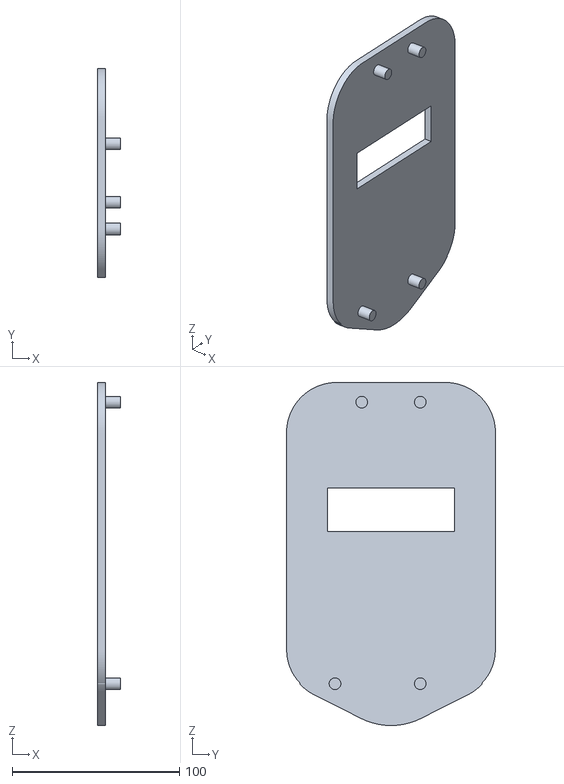
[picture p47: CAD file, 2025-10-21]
3d designs/stls/sensing unit/v2.0/sensing_unit_v2.0 - 2.stl
14.0 x 125.0 x 205.2

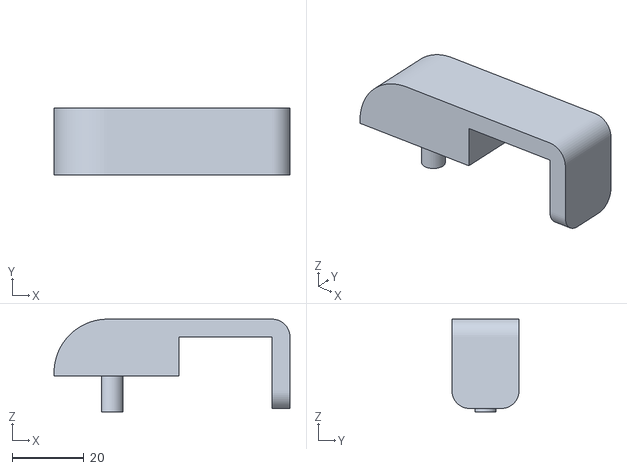
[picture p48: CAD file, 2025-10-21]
3d designs/stls/sensing unit/v2.0/sensing_unit_v2.1 - 3.stl
66.0 x 18.8 x 25.9

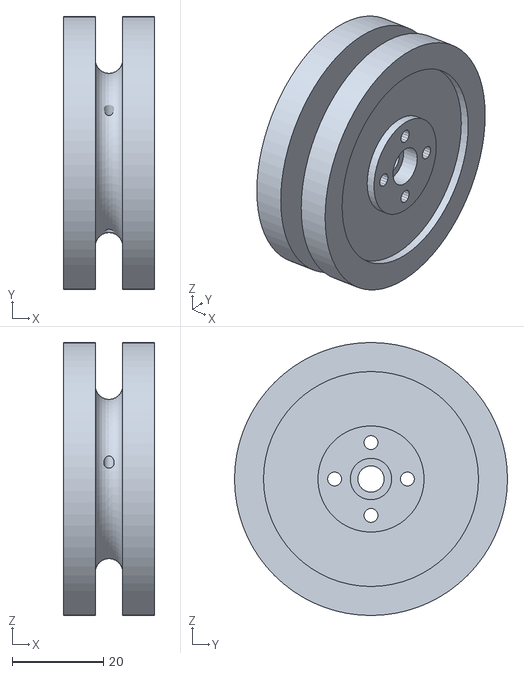
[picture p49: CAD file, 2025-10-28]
3d designs/stls/Pulley v1.0-03.stl
20.0 x 60.0 x 60.0

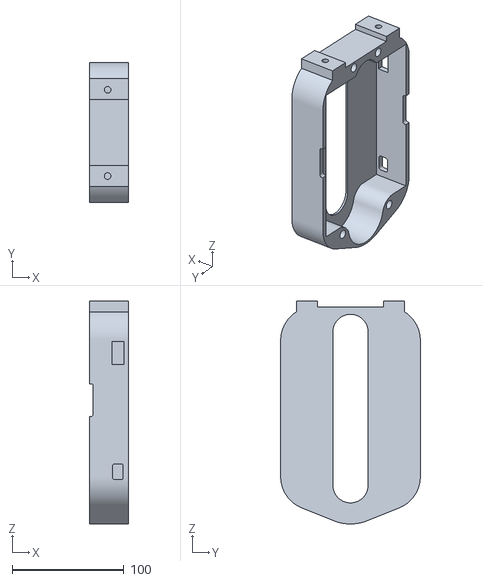
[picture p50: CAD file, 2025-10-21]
3d designs/stls/sensing unit/v2.0/sensing_unit_v2.2 - 1.stl
35.0 x 125.0 x 199.6

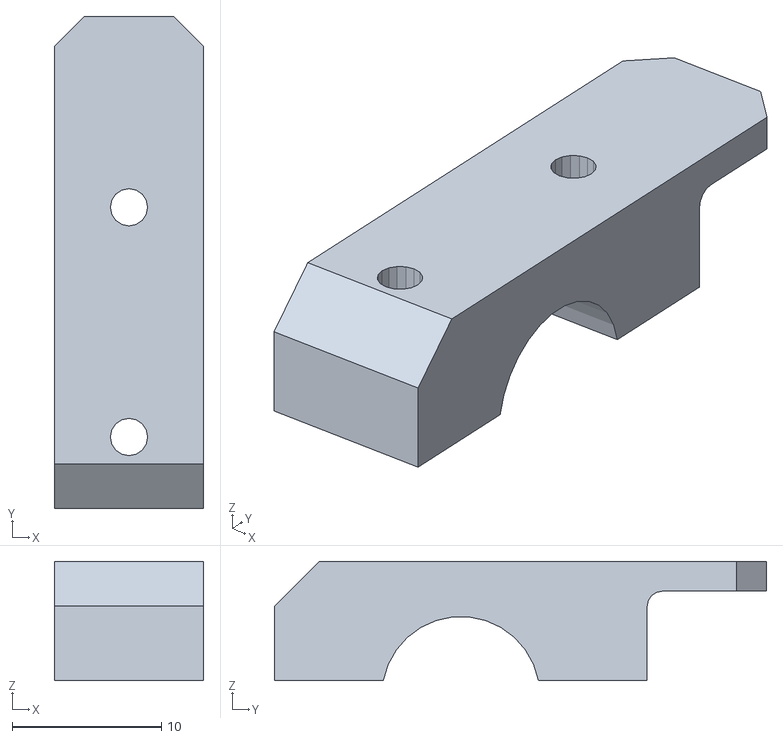
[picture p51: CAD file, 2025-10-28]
3d designs/stls/physics lab part.stl
10.0 x 33.0 x 8.00

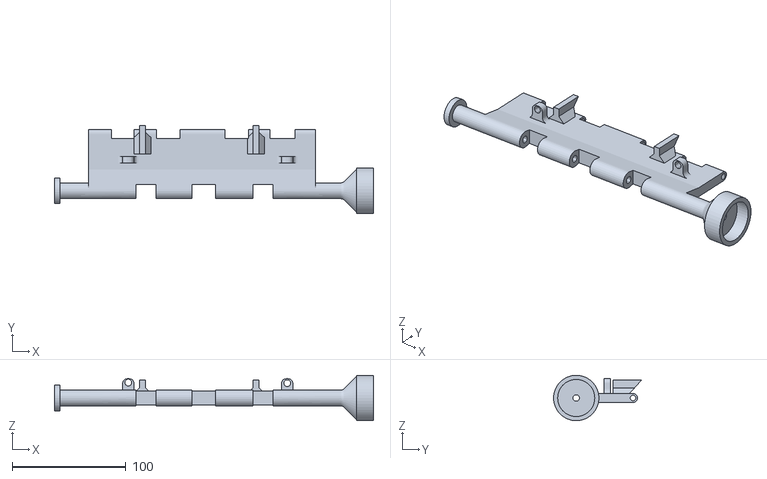
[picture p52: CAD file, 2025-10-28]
3d designs/stls/Bump first side.stl
281.0 x 77.5 x 39.9

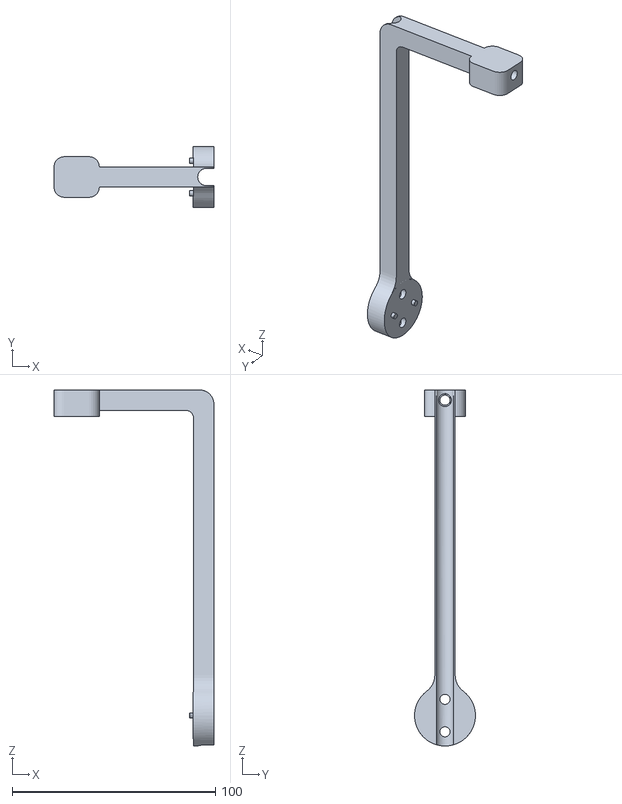
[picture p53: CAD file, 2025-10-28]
3d designs/stls/lamp.stl
78.7 x 30.0 x 175.3

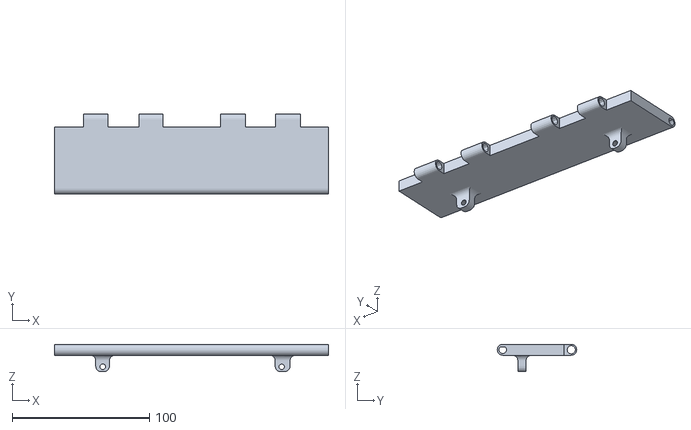
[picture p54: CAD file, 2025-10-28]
3d designs/stls/Damper Second Part.stl
200.0 x 58.0 x 20.0

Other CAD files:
3d designs/stls/Pulley v3.0-02.stl
3d designs/stls/Pulley v3.2.stl
3d designs/stls/first-2.stl
3d designs/stls/stepper holder v1.2.stl
3d designs/stls/39060_txm-standard servo bracket.stl
3d designs/stls/39062_txm-lbrackets.stl
3d designs/stls/39065_TXM-32mmChannel.stl
3d designs/stls/39066_txm-96mmchannel.stl
3d designs/stls/39068_txm-288mmchannel.stl
3d designs/stls/39079_txm-motor shaft hub with set screw.stl
3d designs/stls/39089_txm-motormount.stl
3d designs/stls/39102_txm-stand-offposts6-32x1.stl
3d designs/stls/39107_txm-stand-offposts6-32x32mm.stl
3d designs/stls/39271_TXM-Flat288mmx26mm.stl
3d designs/stls/39273_txm-flat96mmx27mm.stl
3d designs/stls/39274_txm-flat64mmx27mm.stl
3d designs/stls/39300A_TXM-Linear Slide Gear.stl
3d designs/stls/39300B_TXM-Linear Slide Rail.stl
3d designs/stls/39300C_TXM-Linear Slide Bushing.stl
3d designs/stls/40229_txp-6mm shaft set collar.stl
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

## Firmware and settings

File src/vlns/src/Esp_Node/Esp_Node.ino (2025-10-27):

#include <WiFi.h>
#include <ros.h>
#include <std_msgs/Bool.h>
#include <std_msgs/Int32.h>
#include <std_msgs/String.h>

#define load1 16
#define load2 17

#define voltPin 33

#define isCar 23
#define high 22

#define btsPin 32

int bts_v =170;

// ---------- Wi-Fi + ROS ------------
const char* ssid     = "Salman";
const char* password = "00002222";

// ROS master (rosserial TCP server) IP and port
IPAddress server(192, 168, 43, 47);  // RPi IP
const uint16_t serverPort = 11411;




ros::NodeHandle nh;
std_msgs::Bool str_msg;

String mode, last;
int tmp=0 , t=-10000 , last_time=0, vol=0;

void messageCb(const std_msgs::String& msg){
mode = msg.data;
}
void btsCb(const std_msgs::Int32& msg) {
bts_v=msg.data;
}


ros::Publisher chatter("/car_passed", &str_msg);
ros::Subscriber<std_msgs::String> sub("mode", messageCb );
ros::Subscriber<std_msgs::Int32> btss("bts", &btsCb );
char msg_buffer[64];

// ---------- Lobot Servo ------------
#include "LobotSerialServoControl.h"

#define SERVO_SERIAL_RX    35
#define SERVO_SERIAL_TX    12
#define receiveEnablePin   13
#define transmitEnablePin  14

// Use UART2 on ESP32
HardwareSerial LobotUART(2);
LobotSerialServoControl BusServo(LobotUART, receiveEnablePin, transmitEnablePin);

// Servo parameters
const uint8_t SERVO_ID = 2;

// ---------- Motion control ----------
bool start_en = true;
unsigned long last_pub_ms = 0;
const uint32_t pub_interval_ms = 1000;

// Helper: read servo position safely
int readServoPosition(uint8_t id) {
  // Library function returns int; commonly -1 on failure
  int pos = BusServo.LobotSerialServoReadPosition(id);
  return pos;
}

void switch2bump() {
  BusServo.LobotSerialServoMove(SERVO_ID, 500, 200);
  delay(400);
  BusServo.LobotSerialServoStopMove(SERVO_ID);
}

void switch2motor() {
  BusServo.LobotSerialServoMove(SERVO_ID, 800, 200);
  delay(400);
  BusServo.LobotSerialServoStopMove(SERVO_ID);
}

void setup() {
  Serial.begin(115200);
  delay(100);

  // ----- Wi-Fi -----
  Serial.print("Connecting to WiFi");
  WiFi.begin(ssid, password);
  while (WiFi.status() != WL_CONNECTED) {
    delay(500);
    Serial.print(".");
  }
  Serial.println("\nWiFi connected");
  Serial.print("ESP32 IP: ");
  Serial.println(WiFi.localIP());

  // ----- Servo bus init -----
  // Initialize Lobot control (sets direction pins)
  BusServo.OnInit();
  // Bring up UART2 for servo bus
  LobotUART.begin(115200, SERIAL_8N1, SERVO_SERIAL_RX, SERVO_SERIAL_TX);
  delay(200);

  // Optionally move once as in original setup
  BusServo.LobotSerialServoMove(SERVO_ID, 700, 600);
  delay(2000);

  // ----- ROS (rosserial TCP) -----
  nh.getHardware()->setConnection(server, serverPort);
  Serial.println("Attempting ROS connection...");
  nh.initNode();
  nh.advertise(chatter);
  nh.subscribe(sub);
  nh.subscribe(btss);

  pinMode(load1,OUTPUT);
  pinMode(load2,OUTPUT);

  pinMode(voltPin,OUTPUT);

  pinMode(high,OUTPUT);

  pinMode(isCar,INPUT_PULLUP);


  pinMode(btsPin, OUTPUT);

  digitalWrite(load1, 1);
  digitalWrite(load2, 1);
  digitalWrite(high, 1);


  analogWrite(btsPin, bts_v);
  attachInterrupt(digitalPinToInterrupt(isCar),OnLow,FALLING);

}

void loop() {
analogWrite(btsPin, bts_v);


control();
  if(millis()-t>1000 && last_time==1){
    str_msg.data=0;
    last_time=0;
    chatter.publish( &str_msg );
  }
  delay(100);
  nh.spinOnce();
}


void control(){
if (mode != last){
  if (mode == "charge"){
    switch2bump();
    digitalWrite(2,1);
    digitalWrite(load1, 1);
    digitalWrite(load2, 1);
    delay(50);
    }
//
  else if (mode == "discharge"){
    switch2motor();
    digitalWrite(load1, 0);
    digitalWrite(load2, 0);
    delay(50);

    }
    else if (mode == "fast"){
    switch2motor();
    digitalWrite(load1, 1);
    digitalWrite(load2, 1);
    delay(50);

    }
    else if (mode == "maxCharge"){
    switch2bump();
    digitalWrite(load1, 1);
    digitalWrite(load2, 1);
    delay(50);

    }
    last = mode;
    }
    
  }
  
void OnLow()
{
  if((millis()-t>1000 && last_time==0)){
    t = millis();
    str_msg.data=1; 
    last_time=1;
    chatter.publish( &str_msg );

  }

  
}

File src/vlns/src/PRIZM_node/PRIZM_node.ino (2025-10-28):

#include <PRIZM.h>          
#include <ros.h>
#include <std_msgs/String.h>


#include <std_msgs/Bool.h>
#include <std_msgs/Float32.h>

const int isCar =2;
int t=10000, last_time=0;

PRIZM prizm; 
ros::NodeHandle  nh;
std_msgs::Float32 enc;
std_msgs::Bool str_msg;


String mode;
int tmp=0;

void messageCb(const std_msgs::String& msg){
mode = msg.data;
}

ros::Publisher encoder_pub("/energy_storage/encoder", &enc);
ros::Publisher chatter("/car_passed", &str_msg);
ros::Subscriber<std_msgs::String> sub("mode", messageCb );





void setup() {

  Serial.begin(57600);
  prizm.PrizmBegin();         
  nh.initNode();
  nh.subscribe(sub);
  nh.advertise(encoder_pub);
  nh.advertise(chatter);
  delay(300);
  prizm.setMotorPower(2,0);
  delay(300);
  enc.data = 0.0;
  encoder_pub.publish( &enc );
  pinMode(isCar, INPUT_PULLUP);
  attachInterrupt(digitalPinToInterrupt(isCar), onLow, FALLING);
    
}

void control(){

  if (mode == "charge"){
    prizm.setMotorPower(2,0);
    prizm.setRedLED(LOW);
    prizm.setGreenLED(HIGH);
    delay(600);
    prizm.setGreenLED(LOW);
    delay(600);
      prizm.setServoPosition(1,90);  
    }

  else if (mode == "discharge"){
    prizm.setMotorPower(2,0);
    prizm.setRedLED(HIGH);
    prizm.setGreenLED(LOW);
    delay(600);
    prizm.setRedLED(LOW);
    delay(600);
    prizm.setServoPosition(1,30);  
    }
    else if (mode == "fast"){
      delay(200);
    prizm.setMotorPower(2,50);
    prizm.setGreenLED(LOW);
    prizm.setRedLED(HIGH);    
    prizm.setServoPosition(1,90);  
    }
    else if (mode == "maxCharge"){
    prizm.setMotorPower(2,0);
    prizm.setRedLED(LOW);
    prizm.setGreenLED(HIGH);  
    prizm.setServoPosition(1,30);  
  
    }
    tmp = prizm.readEncoderCount(2);
    enc.data = abs(tmp/1000.0);
    encoder_pub.publish( &enc );
    
  }

  
  

void loop() {
control();

if(millis()-t>1500 && last_time==1){
  str_msg.data=0;
  last_time=0;
  chatter.publish(&str_msg);
}
delay(100);
nh.spinOnce();
}

void onLow()
{
  if(millis()-t>1500 && last_time==0){
      t=millis();
      str_msg.data=1;
      last_time=1;
      chatter.publish(&str_msg);
  }
  
}

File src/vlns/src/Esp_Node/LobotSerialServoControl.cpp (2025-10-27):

//
//* FileName:      LobotSerialServoControl.h
//* Company:     Hiwonder
//* Date:          2020/05/13  16:53
// *Last Modification Date: 202005131938
//* www.hiwonder.com

#include "LobotSerialServoControl.h"
#include <Stream.h>

LobotSerialServoControl::LobotSerialServoControl(HardwareSerial &A)
{
  isAutoEnableRT = true;
	isUseHardwareSerial = true;
	SerialX = (Stream*)(&A);
}
LobotSerialServoControl::LobotSerialServoControl(HardwareSerial &A,int receiveEnablePin, int transmitEnablePin)
{
  isAutoEnableRT = false;
  this->receiveEnablePin = receiveEnablePin;
  this->transmitEnablePin = transmitEnablePin;
  
  isUseHardwareSerial = true;
  SerialX = (Stream*)(&A);
}

void LobotSerialServoControl::OnInit(void)
{
  if(!isAutoEnableRT)
  {
    pinMode(receiveEnablePin, OUTPUT);
    pinMode(transmitEnablePin, OUTPUT);
    RxEnable();
  }
}

inline void LobotSerialServoControl::RxEnable(void)
{
  digitalWrite(receiveEnablePin, HIGH);
  digitalWrite(transmitEnablePin, LOW);
}
inline void LobotSerialServoControl::TxEnable(void)
{
  digitalWrite(receiveEnablePin, LOW);
  digitalWrite(transmitEnablePin, HIGH);
}

byte LobotSerialServoControl::LobotCheckSum(byte buf[])
{
  byte i;
  uint16_t temp = 0;
  for (i = 2; i < buf[3] + 2; i++) {
    temp += buf[i];
  }
  temp = ~temp;
  i = (byte)temp;
  return i;
}

void LobotSerialServoControl::LobotSerialServoMove(uint8_t id, int16_t position, uint16_t time)
{
  byte buf[10];
  if(position < 0)
    position = 0;
  if(position > 1000)
    position = 1000;
  buf[0] = buf[1] = LOBOT_SERVO_FRAME_HEADER;
  buf[2] = id;
  buf[3] = 7;
  buf[4] = LOBOT_SERVO_MOVE_TIME_WRITE;
  buf[5] = GET_LOW_BYTE(position);
  buf[6] = GET_HIGH_BYTE(position);
  buf[7] = GET_LOW_BYTE(time);
  buf[8] = GET_HIGH_BYTE(time);
  buf[9] = LobotCheckSum(buf);
  if(isAutoEnableRT == false)
    TxEnable();
  SerialX->write(buf, 10);
}

void LobotSerialServoControl::LobotSerialServoStopMove(uint8_t id)
{
  byte buf[6];
  buf[0] = buf[1] = LOBOT_SERVO_FRAME_HEADER;
  buf[2] = id;
  buf[3] = 3;
  buf[4] = LOBOT_SERVO_MOVE_STOP;
  buf[5] = LobotCheckSum(buf);
  if(isAutoEnableRT == false)
    TxEnable();
  SerialX->write(buf, 6);
}

void LobotSerialServoControl::LobotSerialServoSetID(uint8_t oldID, uint8_t newID)
{
  byte buf[7];
  buf[0] = buf[1] = LOBOT_SERVO_FRAME_HEADER;
  buf[2] = oldID;
  buf[3] = 4;
  buf[4] = LOBOT_SERVO_ID_WRITE;
  buf[5] = newID;
  buf[6] = LobotCheckSum(buf);
  if(isAutoEnableRT == false)
    TxEnable();
  SerialX->write(buf, 7);
  
#ifdef LOBOT_DEBUG
  Serial.println("LOBOT SERVO ID WRITE");
  int debug_value_i = 0;
  for (debug_value_i = 0; debug_value_i < buf[3] + 3; debug_value_i++)
  {
    Serial.print(buf[debug_value_i], HEX);
    Serial.print(":");
  }
  Serial.println(" ");
#endif

}

void LobotSerialServoControl::LobotSerialServoSetMode(uint8_t id, uint8_t Mode, int16_t Speed)
{
  byte buf[10];

  buf[0] = buf[1] = LOBOT_SERVO_FRAME_HEADER;
  buf[2] = id;
  buf[3] = 7;
  buf[4] = LOBOT_SERVO_OR_MOTOR_MODE_WRITE;
  buf[5] = Mode;
  buf[6] = 0;
  buf[7] = GET_LOW_BYTE((uint16_t)Speed);
  buf[8] = GET_HIGH_BYTE((uint16_t)Speed);
  buf[9] = LobotCheckSum(buf);

#ifdef LOBOT_DEBUG
  Serial.println("LOBOT SERVO Set Mode");
  int debug_value_i = 0;
  for (debug_value_i = 0; debug_value_i < buf[3] + 3; debug_value_i++)
  {
    Serial.print(buf[debug_value_i], HEX);
    Serial.print(":");
  }
  Serial.println(" ");
#endif
  if(isAutoEnableRT == false)
    TxEnable();
  SerialX->write(buf, 10);
}

void LobotSerialServoControl::LobotSerialServoLoad(uint8_t id)
{
  byte buf[7];
  buf[0] = buf[1] = LOBOT_SERVO_FRAME_HEADER;
  buf[2] = id;
  buf[3] = 4;
  buf[4] = LOBOT_SERVO_LOAD_OR_UNLOAD_WRITE;
  buf[5] = 1;
  buf[6] = LobotCheckSum(buf);
  if(isAutoEnableRT == false)
    TxEnable();
  SerialX->write(buf, 7);
  
#ifdef LOBOT_DEBUG
  Serial.println("LOBOT SERVO LOAD WRITE");
  int debug_value_i = 0;
  for (debug_value_i = 0; debug_value_i < buf[3] + 3; debug_value_i++)
  {
    Serial.print(buf[debug_value_i], HEX);
    Serial.print(":");
  }
  Serial.println(" ");
#endif

}

void LobotSerialServoControl::LobotSerialServoUnload(uint8_t id)
{
  byte buf[7];
  buf[0] = buf[1] = LOBOT_SERVO_FRAME_HEADER;
  buf[2] = id;
  buf[3] = 4;
  buf[4] = LOBOT_SERVO_LOAD_OR_UNLOAD_WRITE;
  buf[5] = 0;
  buf[6] = LobotCheckSum(buf);
  if(isAutoEnableRT == false)
    TxEnable();
  SerialX->write(buf, 7);
  
#ifdef LOBOT_DEBUG
  Serial.println("LOBOT SERVO LOAD WRITE");
  int debug_value_i = 0;
  for (debug_value_i = 0; debug_value_i < buf[3] + 3; debug_value_i++)
  {
    Serial.print(buf[debug_value_i], HEX);
    Serial.print(":");
  }
  Serial.println(" ");
#endif
}

int LobotSerialServoControl::LobotSerialServoReceiveHandle(byte *ret)
{
  bool frameStarted = false;
  bool receiveFinished = false;
  byte frameCount = 0;
  byte dataCount = 0;
  byte dataLength = 2;
  byte rxBuf;
  byte recvBuf[32];
  byte i;

  while (SerialX->available()) {
    rxBuf = SerialX->read();
    delayMicroseconds(100);
    if (!frameStarted) {
      if (rxBuf == LOBOT_SERVO_FRAME_HEADER) {
        frameCount++;
        if (frameCount == 2) {
          frameCount = 0;
          frameStarted = true;
          dataCount = 1;
        }
      }
      else {
        frameStarted = false;
        dataCount = 0;
        frameCount = 0;
      }
    }
    if (frameStarted) {
      recvBuf[dataCount] = (uint8_t)rxBuf;
      if (dataCount == 3) {
        dataLength = recvBuf[dataCount];
        if (dataLength < 3 || dataCount > 7) {
          dataLength = 2;
          frameStarted = false;
        }
      }
      dataCount++;
      if (dataCount == dataLength + 3) {
        
#ifdef LOBOT_DEBUG
        Serial.print("RECEIVE DATA:");
        for (i = 0; i < dataCount; i++) {
          Serial.print(recvBuf[i], HEX);
          Serial.print(":");
        }
        Serial.println(" ");
#endif

        if (LobotCheckSum(recvBuf) == recvBuf[dataCount - 1]) {
          
#ifdef LOBOT_DEBUG
          Serial.println("Check SUM OK!!");
          Serial.println("");
#endif

          frameStarted = false;
          memcpy(ret, recvBuf + 4, dataLength);
          return 1;
        }
        return -1;
      }
    }
  }
}

int LobotSerialServoControl::LobotSerialServoReadPosition(uint8_t id)
{
  int count = 10000;
  int ret;
  byte buf[6];

  buf[0] = buf[1] = LOBOT_SERVO_FRAME_HEADER;
  buf[2] = id;
  buf[3] = 3;
  buf[4] = LOBOT_SERVO_POS_READ;
  buf[5] = LobotCheckSum(buf);
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

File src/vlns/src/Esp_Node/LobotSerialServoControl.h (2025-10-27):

//
//* FileName:      LobotSerialServoControl.h
//* Company:     Hiwonder
//* Date:          2020/05/13  16:53
// *Last Modification Date: 202005131938
//* www.hiwonder.com
//

#ifndef LOBOTSERIALSERVOCONTROL_H
#define LOBOTSERIALSERVOCONTROL_H

#include <Arduino.h>

#define GET_LOW_BYTE(A) (uint8_t)((A))
//宏函数 获得A的低八位
#define GET_HIGH_BYTE(A) (uint8_t)((A) >> 8)
//宏函数 获得A的高八位
#define BYTE_TO_HW(A, B) ((((uint16_t)(A)) << 8) | (uint8_t)(B))
//宏函数 以A为高八位 B为低八位 合并为16位整形


#define LOBOT_SERVO_FRAME_HEADER         0x55

#define LOBOT_SERVO_MOVE_TIME_WRITE      1
#define LOBOT_SERVO_MOVE_TIME_READ       2
#define LOBOT_SERVO_MOVE_TIME_WAIT_WRITE 7
#define LOBOT_SERVO_MOVE_TIME_WAIT_READ  8
#define LOBOT_SERVO_MOVE_START           11
#define LOBOT_SERVO_MOVE_STOP            12
#define LOBOT_SERVO_ID_WRITE             13
#define LOBOT_SERVO_ID_READ              14
#define LOBOT_SERVO_ANGLE_OFFSET_ADJUST  17
#define LOBOT_SERVO_ANGLE_OFFSET_WRITE   18
#define LOBOT_SERVO_ANGLE_OFFSET_READ    19
#define LOBOT_SERVO_ANGLE_LIMIT_WRITE    20
#define LOBOT_SERVO_ANGLE_LIMIT_READ     21
#define LOBOT_SERVO_VIN_LIMIT_WRITE      22
#define LOBOT_SERVO_VIN_LIMIT_READ       23
#define LOBOT_SERVO_TEMP_MAX_LIMIT_WRITE 24
#define LOBOT_SERVO_TEMP_MAX_LIMIT_READ  25
#define LOBOT_SERVO_TEMP_READ            26
#define LOBOT_SERVO_VIN_READ             27
#define LOBOT_SERVO_POS_READ             28
#define LOBOT_SERVO_OR_MOTOR_MODE_WRITE  29
#define LOBOT_SERVO_OR_MOTOR_MODE_READ   30
#define LOBOT_SERVO_LOAD_OR_UNLOAD_WRITE 31
#define LOBOT_SERVO_LOAD_OR_UNLOAD_READ  32
#define LOBOT_SERVO_LED_CTRL_WRITE       33
#define LOBOT_SERVO_LED_CTRL_READ        34
#define LOBOT_SERVO_LED_ERROR_WRITE      35
#define LOBOT_SERVO_LED_ERROR_READ       36


class LobotSerialServoControl {
  public:
	  LobotSerialServoControl(HardwareSerial &A);
    LobotSerialServoControl(HardwareSerial &A,int receiveEnablePin, int transmitEnablePin);
    void OnInit(void);
    void LobotSerialServoMove(uint8_t id, int16_t position, uint16_t time);
    void LobotSerialServoStopMove(uint8_t id);
    void LobotSerialServoSetID(uint8_t oldID, uint8_t newID);
    void LobotSerialServoSetMode(uint8_t id, uint8_t Mode, int16_t Speed);
    void LobotSerialServoLoad(uint8_t id);
    void LobotSerialServoUnload(uint8_t id);
    int LobotSerialServoReceiveHandle(byte *ret);
    int LobotSerialServoReadPosition(uint8_t id);
    int LobotSerialServoReadVin(uint8_t id);


  protected:
    byte LobotCheckSum(byte buf[]);
    inline void RxEnable(void);
    inline void TxEnable(void);
      
  protected:
	  bool isUseHardwareSerial;
    Stream *SerialX;
    bool isAutoEnableRT;
    int receiveEnablePin;
    int transmitEnablePin;
  
};

#endif

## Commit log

2025-10-21 3D Designs Stl
    [39060_txm-standard servo bracket.stl, 39062_txm-lbrackets.stl, 39065_TXM-32mmChannel.stl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]
2025-10-28 Web Dashboard: Full Source Code
    [chatter_log.csv]
2025-10-28 3D Files Upload
    [Bearing to tetrix v1.0-01.stl, Bearing to tetrix v1.0-02.stl, Bump first side.stl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]
2025-10-28 Delete src/Web Dashboard/chatter_log.csv
    Old version
    [chatter_log.csv]
2025-10-31 3d parts image
    [first.stl, kotlee.stl, second.stl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]
